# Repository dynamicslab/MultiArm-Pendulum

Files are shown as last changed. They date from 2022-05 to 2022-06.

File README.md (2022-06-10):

# The Experimental Multi-Arm Pendulum on a Cart

## Overview:
This repository is for our paper: "*[The Experimental Multi-Arm Pendulum on a Cart: A Benchmark System for Chaos, Learning, and Control.](https://arxiv.org/abs/2205.06231)*" The following figure shows an overview of the experimental system.

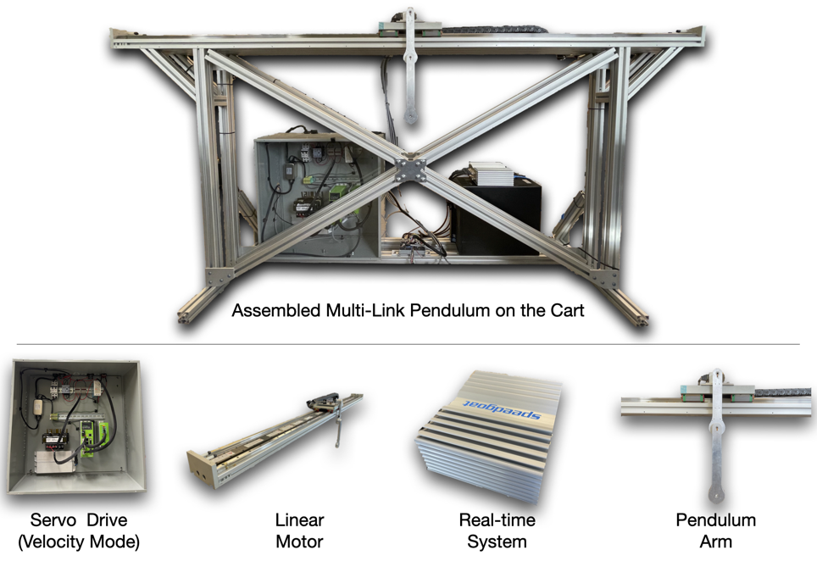
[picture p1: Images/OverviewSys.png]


This repository contains the following files:
- All the CAD files needed to build the pendulum hardware.
- Link to the user's manuals that correspond to some of the parts we used.
- The experimental data sets of the **single, double, and triple pendulum** with and without external excitation. We believe this data set will be extremely useful for the Machine Learning and AI community to test their modeling algorithm. The slow-motion video data for the double pendulum can be accessed using this **[Link](http://doi.org/10.5281/zenodo.6633719)**.
- A demo file for setting up the hardware system and using it for data collection.
- Demo files for parameter estimation of the **single, double, and triple pendulum**.

## Cite:
If you find our data set or hardware useful for your research, please kindly cite it as: 

@misc{kaheman2022experimental,
      title={The Experimental Multi-Arm Pendulum on a Cart: A Benchmark System for Chaos, Learning, and Control}, 
      author={Kadierdan Kaheman and Urban Fasel and Jason J. Bramburger and Benjamin Strom and J. Nathan Kutz and Steven L. Brunton},
      year={2022},
      eprint={2205.06231},
      archivePrefix={arXiv},
      primaryClass={nlin.CD}
}

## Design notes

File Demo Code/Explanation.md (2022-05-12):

# This folder contains files needed for data collection and control of the triple pendulum on the cart system.

This folder contains following files:
- EncoderReading.slx: This Simulink file is used to record the sensor data and control the linear motor.
- speedgoat_IO392_50k_CI_02385.mat: This is the Bitstream file needed to configure the Speedgoat system's IO-392 module.

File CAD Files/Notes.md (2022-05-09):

# Notes:

- The author thanks HIWIN for providing the CAD file of their linear motor. 
- Some CAD files are downloaded from McMaster.com, and the author does not claim any copyrights on those files.

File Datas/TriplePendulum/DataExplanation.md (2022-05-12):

# This folder contains the experimental data gathered from the triple pendulum system.

This folder contains following files:
- TripleDataFreeSwing_X_Dt_0_0001.mat: These files record the rotational angle and velocity of the triple pendulum with zero cart movement. The sampling rate is dt=0.0001(s).
- TripleDataWithControl_X_Dt_0_0001.mat: These files record the rotational angle and velocity of the triple pendulum with pendulum cart moving back and forth. The cart position and velocity are also recorded. The sampling rate is dt=0.0001(s).

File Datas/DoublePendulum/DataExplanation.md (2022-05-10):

# This folder contains data set of double pendulum.

- DoubleDataFreeSwing_X_Dt_0_001.mat: Those files contains the data set recorded during the double pendulum freee-swing experiments. Dring the experiments the pendulum cart is mounted and won't move. The angular position and velocity of the pendulum arm is recorded.
- DoubleDataWithControl_X_Dt_0_0001.mat: Those files contains the data set recorded during the double pendulum experiments with control input. Two extra measurements, pendulum cart position and velocity are given.

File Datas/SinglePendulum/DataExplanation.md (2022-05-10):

# This folder contains the experimental data of the single pendulum on the cart system.

This folder contains the following files:
- SingleDataFreeSwing_1_Dt_0_0001.mat: This file contains recordings of the free-swing experiment of the single pendulum. The sampling time is dt=0.0001, with the pendulum cart mounted.
- SingleDataWithControl_1_Dt_0_0001.mat: This file cintains the recording of the single pendulum on the cart system with the cart moving back and forth. The sampling time is dt=0.0001. The movement of the cart along wih its velocity is stored in the "Distance" and "Velocity" structure.
- SingleDataWithControl_2_Dt_0_0001.mat: This file cintains the recording of the single pendulum on the cart system with the cart moving back and forth. The sampling time is dt=0.0001. The movement of the cart along wih its velocity is stored in the "Distance" and "Velocity" structure.

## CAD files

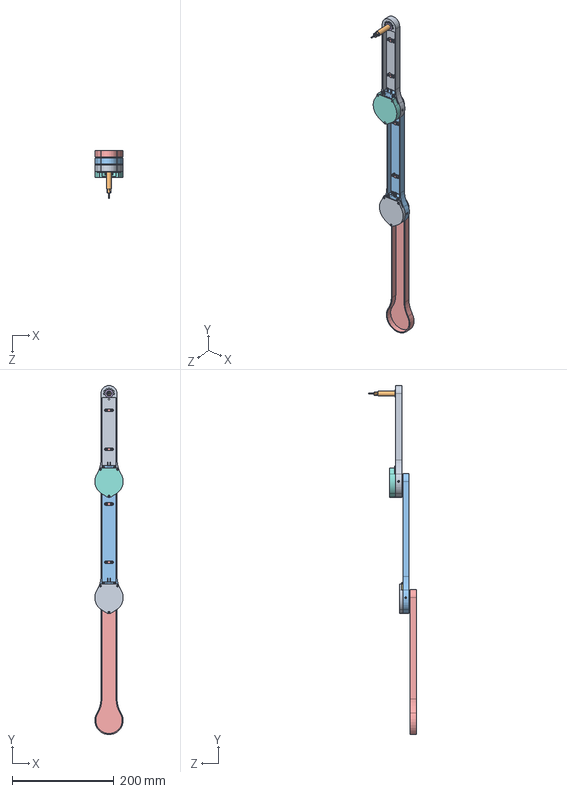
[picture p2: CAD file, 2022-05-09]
CAD Files/ArmsAssembly.SLDASM
55.9 x 686.3 x 93.5 mm
Arm1
Arm1Shaft
Arm2
Arm2Shaft
Arm3
Arm3Shaft
BearingPlate x 2
BrushBlock-5
BrushShim
EncoderShim x 2
SlipRing5Channel
SlipRing8Channel
WireClip x 4
91251A077_Black-Oxide Alloy Steel Socket Head Screw x 14
91251A081_Black-Oxide Alloy Steel Socket Head Screw x 4
3088A449_1008-1010 Carbon Steel Ring Shims x 2
R188 x 4
97022A213_316 Stainless Steel Ring Shim x 2
EM2-X-X-X x 2
HUBDISK-2-X-250-X x 2
98126A447_18-8 Stainless Steel Ring Shim x 2
98055A122_1074-1095 Spring Steel Ring Shim
97633A130_External Retaining Ring x 2
Arm1Cover
Arm2Cover

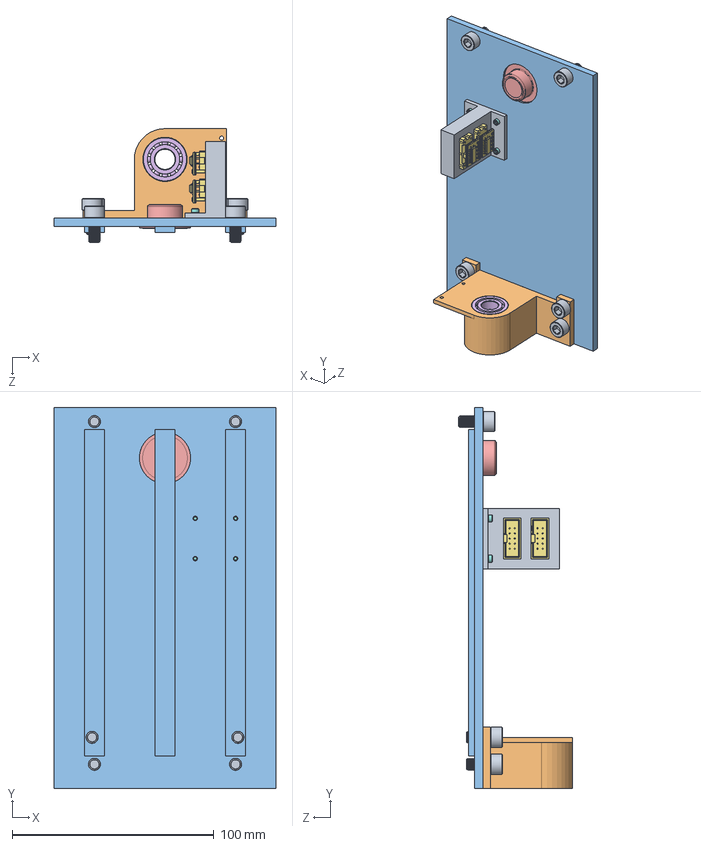
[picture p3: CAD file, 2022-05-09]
CAD Files/CartPlateAssemble.SLDASM
110.0 x 189.0 x 56.5 mm
DriverClip
BearingHousing
CartPlate
Spacer
3329A31_Surface-Mount Circular Mountable Level
5972K241_Ball Bearing x 2
PC4-H10_SolidWorks x 2
91251A077_Black-Oxide Alloy Steel Socket Head Screw x 4
96144A111_Fine-Thread Alloy Steel Socket Head Screw x 6

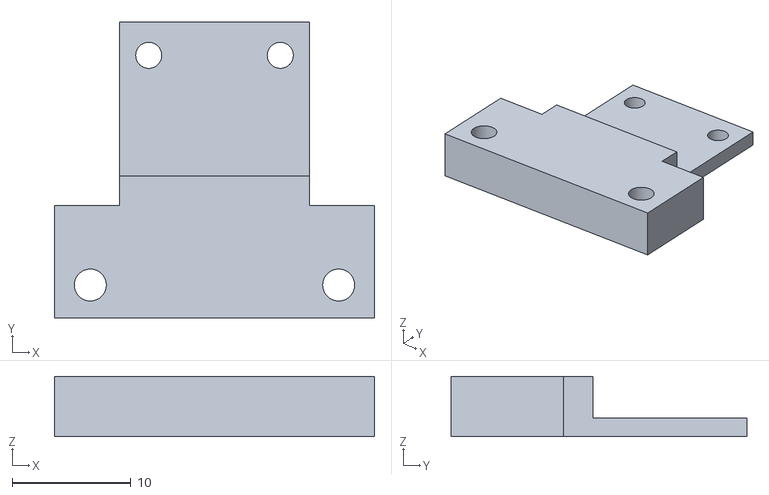
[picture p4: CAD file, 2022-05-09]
CAD Files/3D Printed Parts/BlockBase.STL
27.0 x 25.0 x 5.08

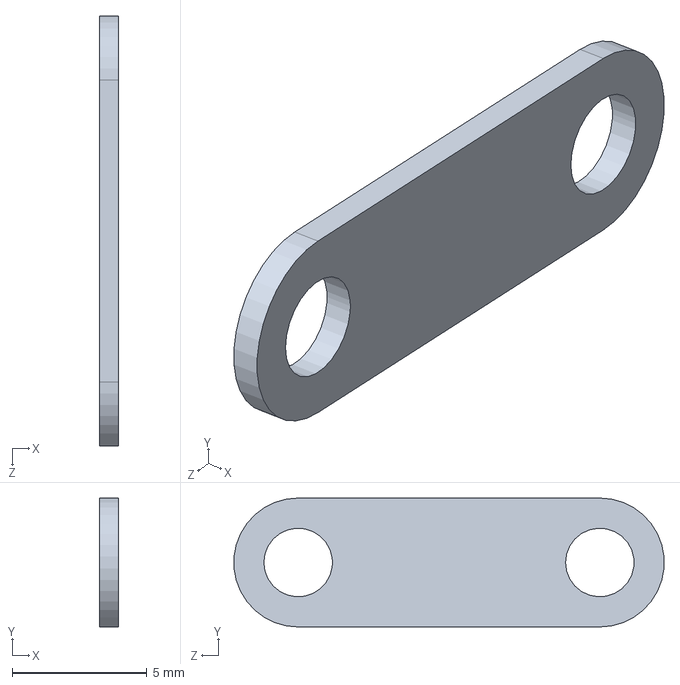
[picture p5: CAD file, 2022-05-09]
CAD Files/Parts/BrushShim.SLDPRT
0.711 x 4.78 x 15.9 mm

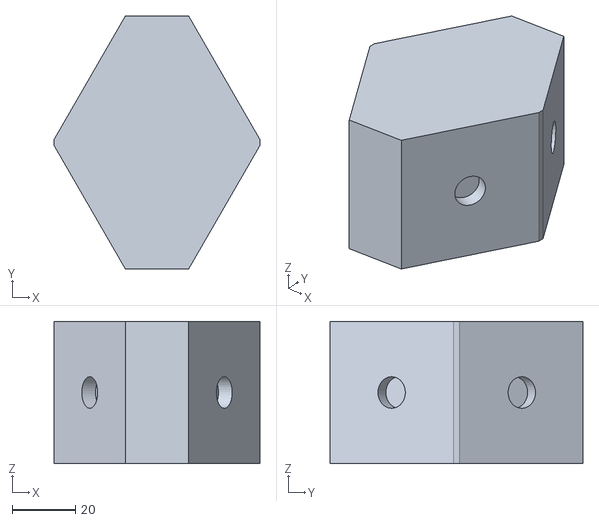
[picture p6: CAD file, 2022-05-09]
CAD Files/3D Printed Parts/AlignTool2.STL
65.0 x 79.9 x 45.0

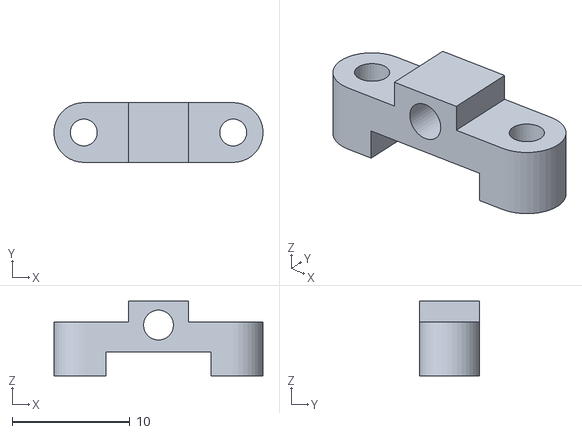
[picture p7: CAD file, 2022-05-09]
CAD Files/3D Printed Parts/WireClip.STL
17.8 x 5.08 x 6.35

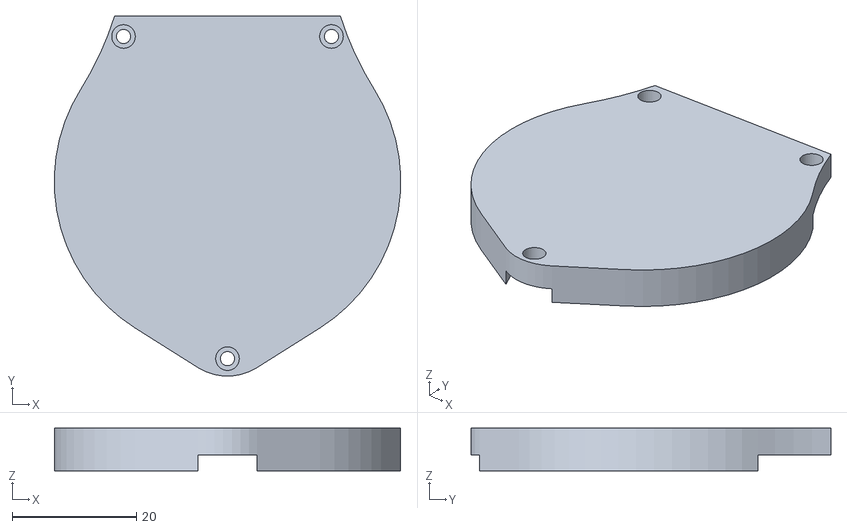
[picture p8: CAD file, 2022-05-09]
CAD Files/3D Printed Parts/Arm2Cover.STL
55.8 x 58.0 x 6.86

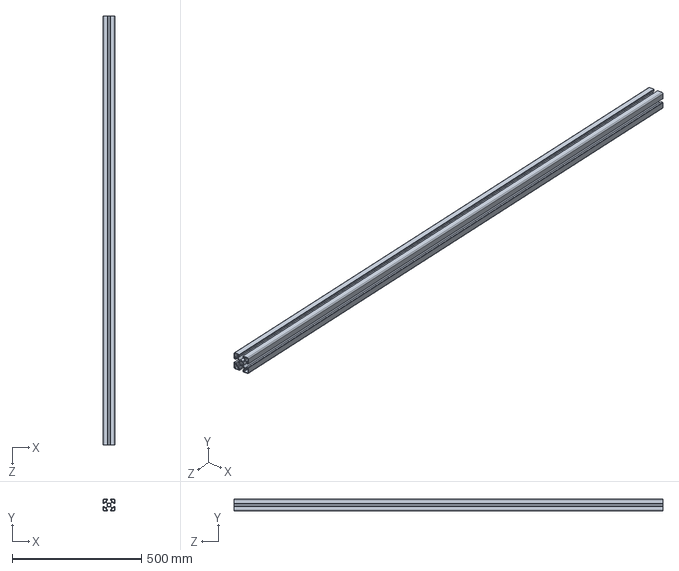
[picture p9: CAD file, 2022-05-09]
CAD Files/Parts/Extrusion6.SLDPRT
45.0 x 45.0 x 1658.5 mm

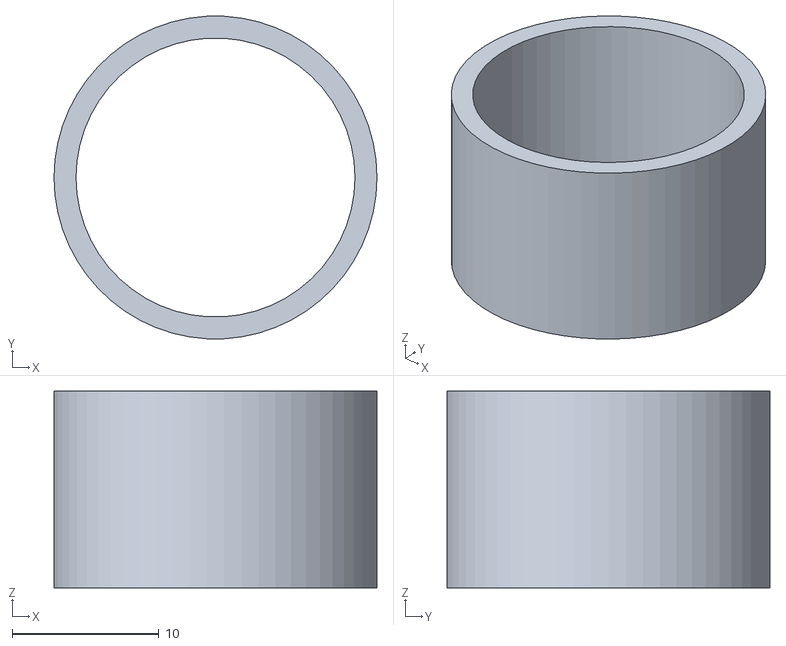
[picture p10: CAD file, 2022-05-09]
CAD Files/3D Printed Parts/Spacer.STL
22.0 x 22.0 x 13.4

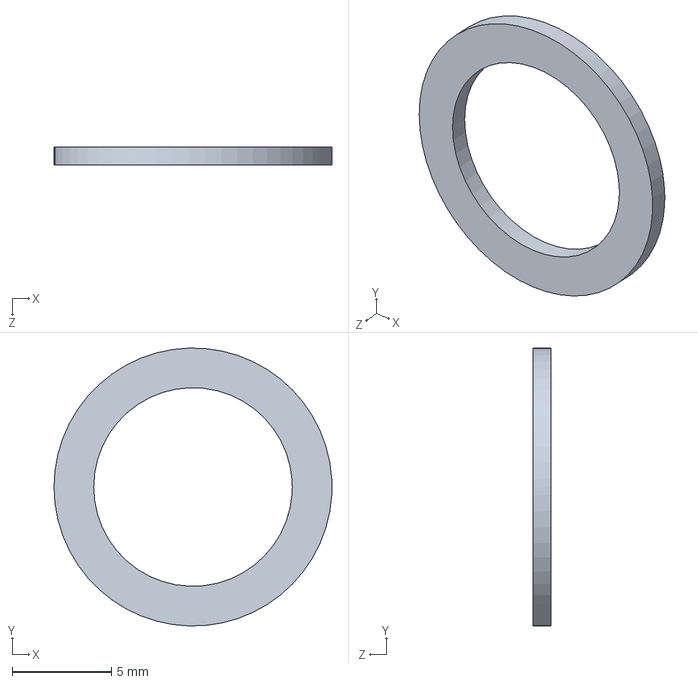
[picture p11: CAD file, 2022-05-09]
CAD Files/Parts/3DPrintedShim.SLDPRT
14.0 x 14.0 x 0.93 mm

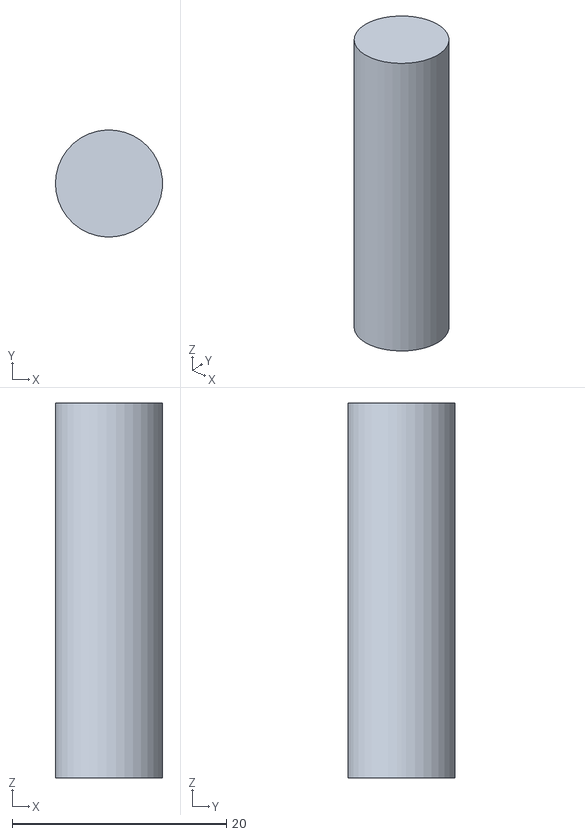
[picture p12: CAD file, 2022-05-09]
CAD Files/3D Printed Parts/AlignTool1.STL
10.0 x 9.99 x 35.0

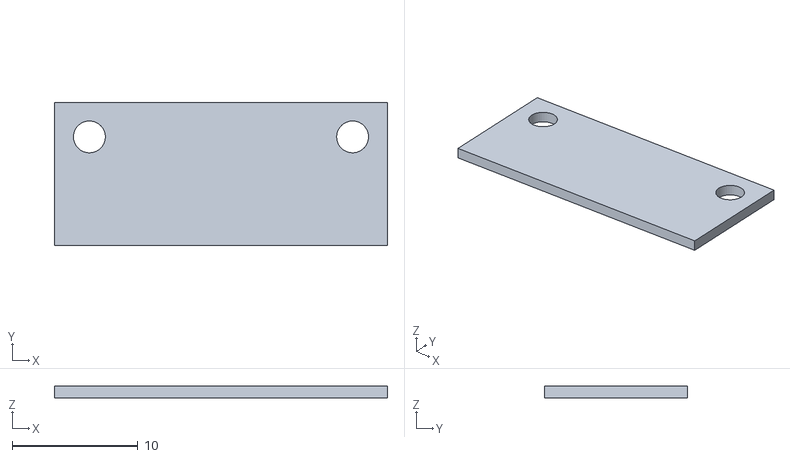
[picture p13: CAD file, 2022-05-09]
CAD Files/3D Printed Parts/EncoderShim.STL
26.5 x 11.4 x 0.965

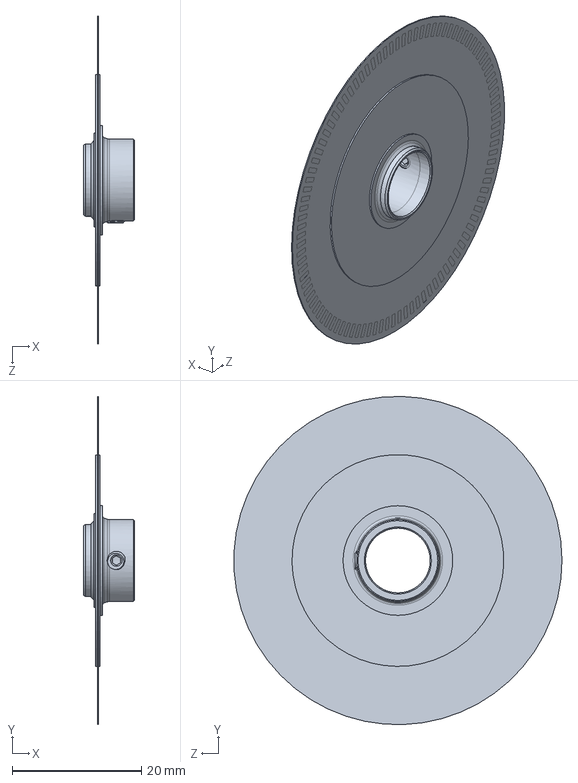
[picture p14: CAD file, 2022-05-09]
CAD Files/Parts/HUBDISK-2-X-394-X.SLDPRT
7.87 x 50.8 x 50.8 mm

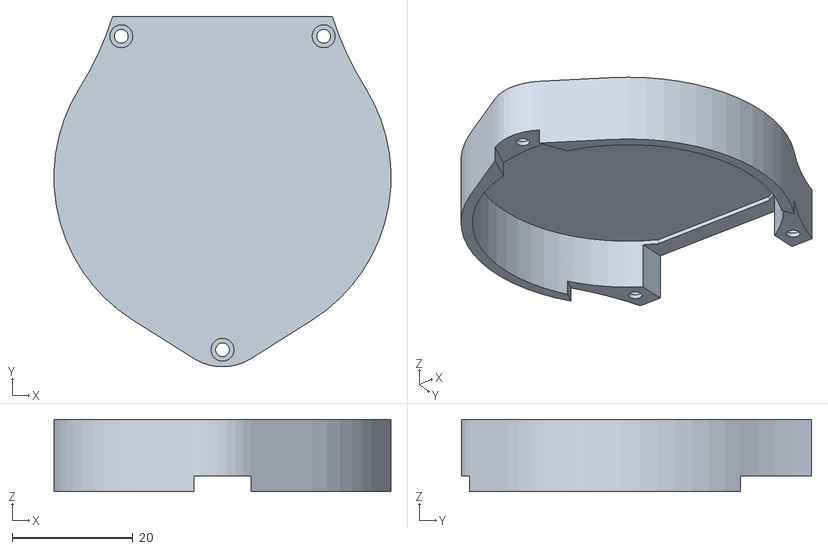
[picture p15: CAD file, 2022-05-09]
CAD Files/3D Printed Parts/Arm1Cover.STL
55.8 x 58.0 x 11.9

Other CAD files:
CAD Files/3D Printed Parts/DriverClip.STL
CAD Files/3D Printed Parts/BrushShim.STL
CAD Files/Parts/Arm3.SLDPRT
CAD Files/Parts/R188.SLDPRT
CAD Files/Drawing/Arm1.SLDDRW
CAD Files/Drawing/Arm1Shaft.SLDDRW
CAD Files/Drawing/Arm2.SLDDRW
CAD Files/Drawing/Arm2Shaft.SLDDRW
CAD Files/Drawing/Arm3.SLDDRW
CAD Files/Drawing/Arm3Shaft.SLDDRW
CAD Files/Drawing/BearingHousing.SLDDRW
CAD Files/Drawing/BearingPlate.SLDDRW
CAD Files/Drawing/CartPlate.SLDDRW
CAD Files/Drawing/XConnector.SLDDRW
CAD Files/Parts/3088A449_1008-1010 Carbon Steel Ring Shims.SLDPRT
CAD Files/Parts/3329A31_Surface-Mount Circular Mountable Level.SLDPRT
CAD Files/Parts/47065T83_70 lb. Capacity Plate Mount Swivel Caster for T-Slotted Framing.SLDPRT
CAD Files/Parts/47065T948_T-Slotted Framing (1).SLDPRT
CAD Files/Parts/47065T998_T-Slotted Framing.SLDPRT
CAD Files/Parts/5537T134_T-Slotted Framing.SLDPRT
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

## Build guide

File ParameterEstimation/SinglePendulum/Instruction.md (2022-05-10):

# This folder contains the files for the parameter estimation of the single pendulum.

The purpose of the files are listed as follows:
- SinglePendulumArm_RawData_1.mat: This is the raw data we collected from the single pendulum free-swing experiment. During the experiments, the cart of the pendulum is fixed and the rotational angle and velocity of the pendulum arm is recorded. The first signal of the "data" structure is the rotational angle, while the second one represents the rotational velocity.
- PrepareDataForSinglePendulumParameterEstimation.m: This file process the above raw data and trim it into the correct format for parameter estimation. Moreover, it also allows the user to perform nosie filtering on the velocity data of the single pendulum. The this script will generate a file named "SinglePendulumDataForParameterEstimation.mat", which will be used for parameter estimation.
- SinglePendulumDataForParameterEstimation.mat: Mat file generated by above script. This mat file contains the data that will be used for parameter estimation and validation.
- OptimizeParameter_SinglePendulum.mlx: This script is used to solve the optimization problem that identifies the parameters of the single pendulum.
- ObjectiveFuntion_SinglePendulumParameterEstimation.m: This file define the optimization problem needed for the parameter estimation of the single pendulum.
- EstimatedParameters_SinglePendulum.mat: This files contains the estimated parameters of the single pendulum. For details on the meaning of the values and its units, please check the "OptimizeParameter_SinglePendulum.mlx" file.
- SinglePendulumSymbolicCalculation.m: This file derives the equation of motion of the single pendulum. The derived ODE will be used for parameter estimation.
- SinglePendulumODE.m: This file is the derived ODE of the single pendulum.

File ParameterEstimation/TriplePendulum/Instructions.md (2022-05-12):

# This folder contains files for the parameter estimation of the triple pendulum.

This folder contains following files:
- TriplePendulumData_Raw.mat: Experimental data gather from the triple pendulum free-swing moton, with sampling rate of dt=0.001. This file will be processed by "PrepareDataForTriplePendulumParameterEstimation.m" to get rid of the noise in the derivative measurements. Then it will be trimed into pieces and stored into a cell array.
- PrepareDataForTriplePendulumParameterEstimation.m: This file is used to process the "TriplePendulumData_Raw.mat" file so that it can be used for parameter estimation.
- TriplePendulumSymbolicCalculation.m: This file is usd to calculate the ODE of the triple pendulum via symbolic toolbox of Matlab.
- TriplePendulumODE_Mounted.m: This file is the ODE file of the triple pendulum. It can used used to simulate the behavior of the triple pendulum.
- TriplePendulumSimWithX0.m: This file is used to simulate the ODE of the triple pendulum given some user define initial condition of triple pendulum.
- ObjectiveFuntion_TriplePendulumParameterEstimation.m: This file is used to define the objective function of the parameter estimation problem of the triple pendulum.
- OptimizeParameter_TriplePendulum.mlx: This file is used to solve the prameter estimation problem of the triple pndulum. It will also save the estimated parameters of the triple pendulum.
-  EstimatedParameters_TriplePendulum.mat: This file stores the estimated parameters of the triple pendulum. For their meaning, please check the "OptimizeParameter_TriplePendulum.mlx" file.

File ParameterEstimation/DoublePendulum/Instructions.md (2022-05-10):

# This folder contains files for estimating the parameters of double pendulum.

The files contained in this folders are:
- DoublePendulumData_Raw.mat: The raw data collected from the double pendulum free-swing experiments. The sampling rate used is dt=0.001s and the pendulum cart is mounted when recording the data. This file is used by "PrepareDataForDoublePendulumParameterEstimation.m" to generated processed double pendulum data for parameter estimation.
- PrepareDataForDoublePendulumParameterEstimation.m: This file is used to chop the raw double pendulum data into pieces. Those pieces of data are stored into a cell array for parameter estimation and validation. The training data and validation data are stored in the "DoublePendulumDataForParameterEstimation.mat" file.
- DoublePendulumDataForParameterEstimation.mat: The data used for parameter estimation and validation.
- ObjectiveFuntion_DoublePendulumParameterEstimation.m: The objective function for the parameter estimation.
- OptimizeParameter_DoublePendulum.mlx: The Matlab script that solves the parameter estimation problem.
- DoublePendulumODE_Mounted.m: The ODE files for simulating the mounted double pendulum. This file is used in the objection file.
- EstimatedParameters_DoublePendulum.mat: The estimated values of double pendulum arm's parameters.
- DoublePendulumSymbolicCalculation.m: The symbolic calculation file needed for deriving the ODEs of double pendulum.

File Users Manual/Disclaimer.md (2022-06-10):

# The author does not claim copyrights on the documentation/user manual shown in this folder. All right belongs to the manufacturer who wrote those documentations. Those files are downloaded from the product's website.

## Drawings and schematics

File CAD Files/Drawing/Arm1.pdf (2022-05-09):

0.433

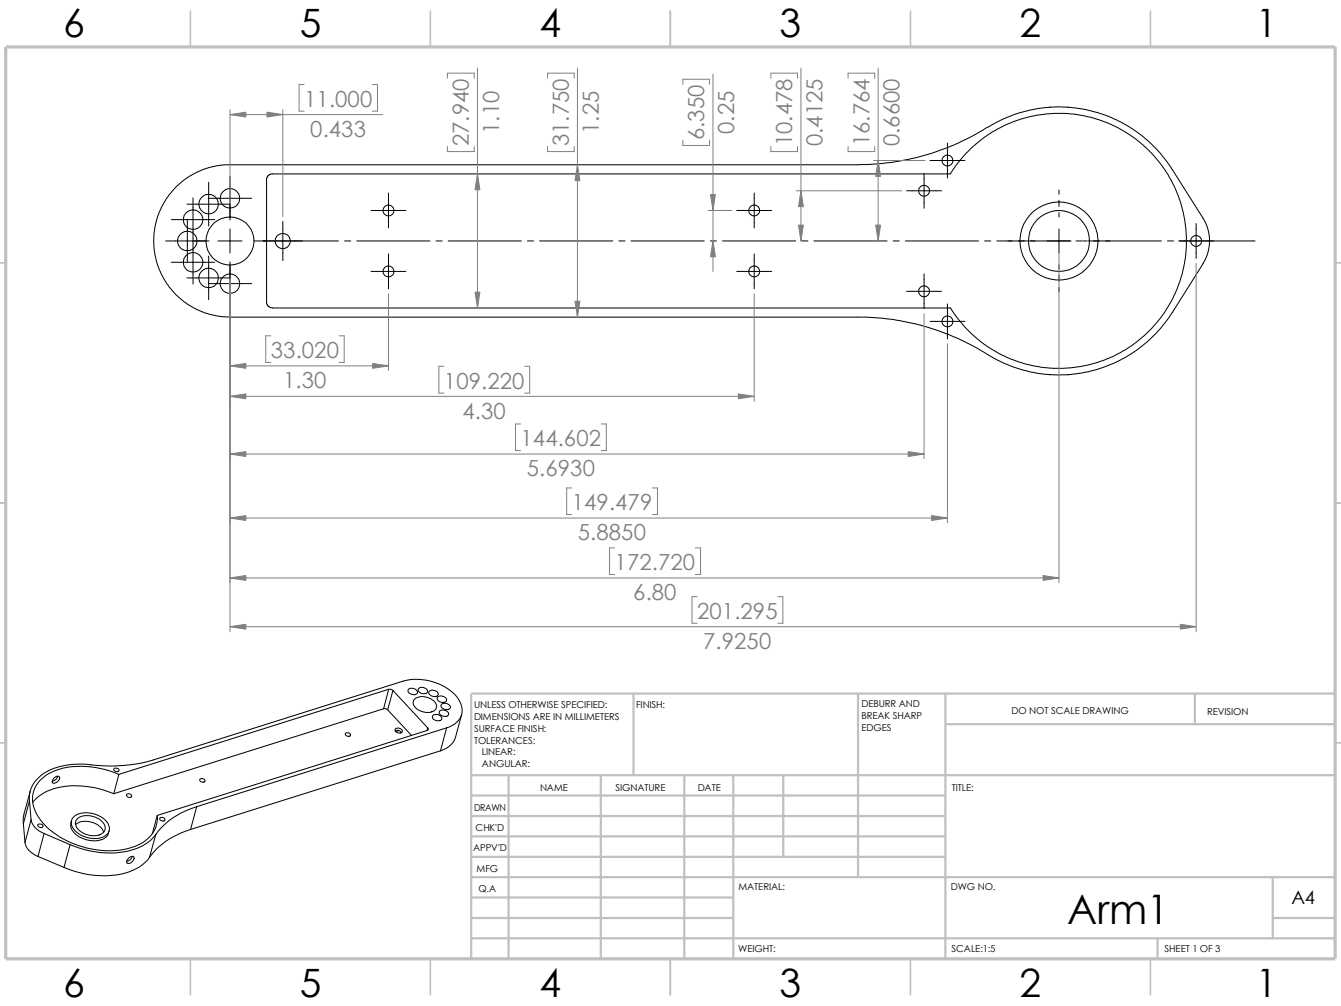
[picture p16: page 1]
REVISION; SCALE:1:5; SHEET 1 OF 3; WEIGHT:; EDGES; FINISH:; DEBURR AND BREAK SHARP; Arm1 ³¹.750

UNLESS OTHERWISE SPECIFIED:
DIMENSIONS ARE IN MILLIMETERS
SURFACE FINISH:
TOLERANCES:
LINEAR:
ANGULAR:

DO NOT SCALE DRAWING

NAME | SIGNATURE | DATE | | | | TITLE:

DRAWN
CHK'D
APPV'D

MFG
Q.A | | | | MATERIAL: | DWG NO. | A4

A A

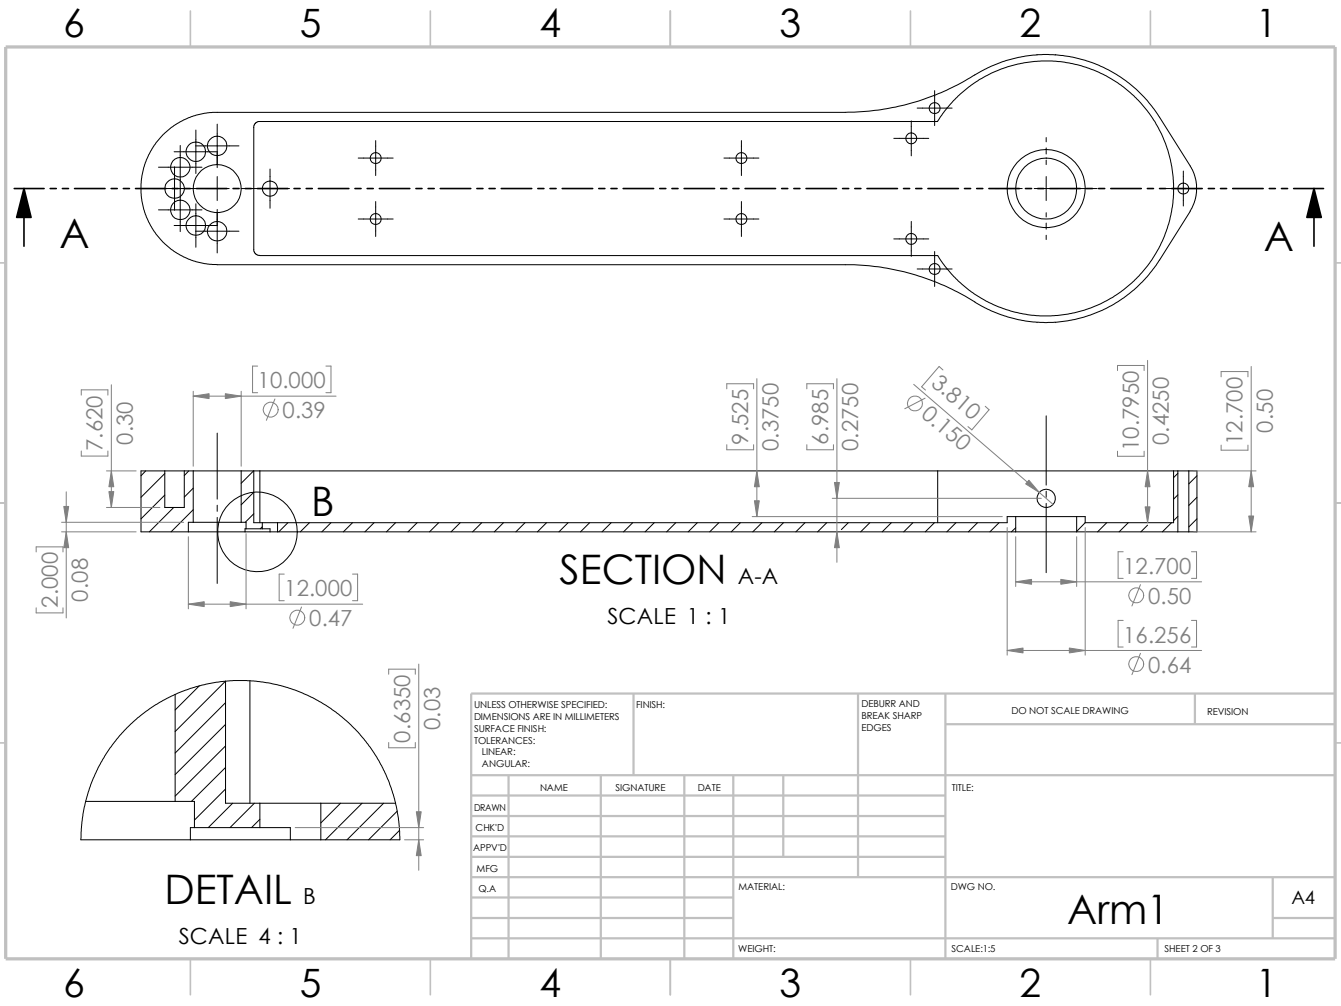
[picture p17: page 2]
DETAIL B; SCALE 4 : 1; SECTION A-A; SCALE; FINISH:; EDGES; DO NOT SCALE DRAWING; REVISION; SCALE:1:5; WEIGHT:; SHEET 2 OF 3; APPV'D; DEBURR AND BREAK SHARP

UNLESS OTHERWISE SPECIFIED:
DIMENSIONS ARE IN MILLIMETERS
SURFACE FINISH:
TOLERANCES:
LINEAR:
ANGULAR:

NAME | SIGNATURE | DATE | TITLE:

CHK'D DRAWN

MFG
Q.A | MATERIAL: | DWG NO. Arm1 | A4

# Uniformly Distributed

# For 2-56 Bolts

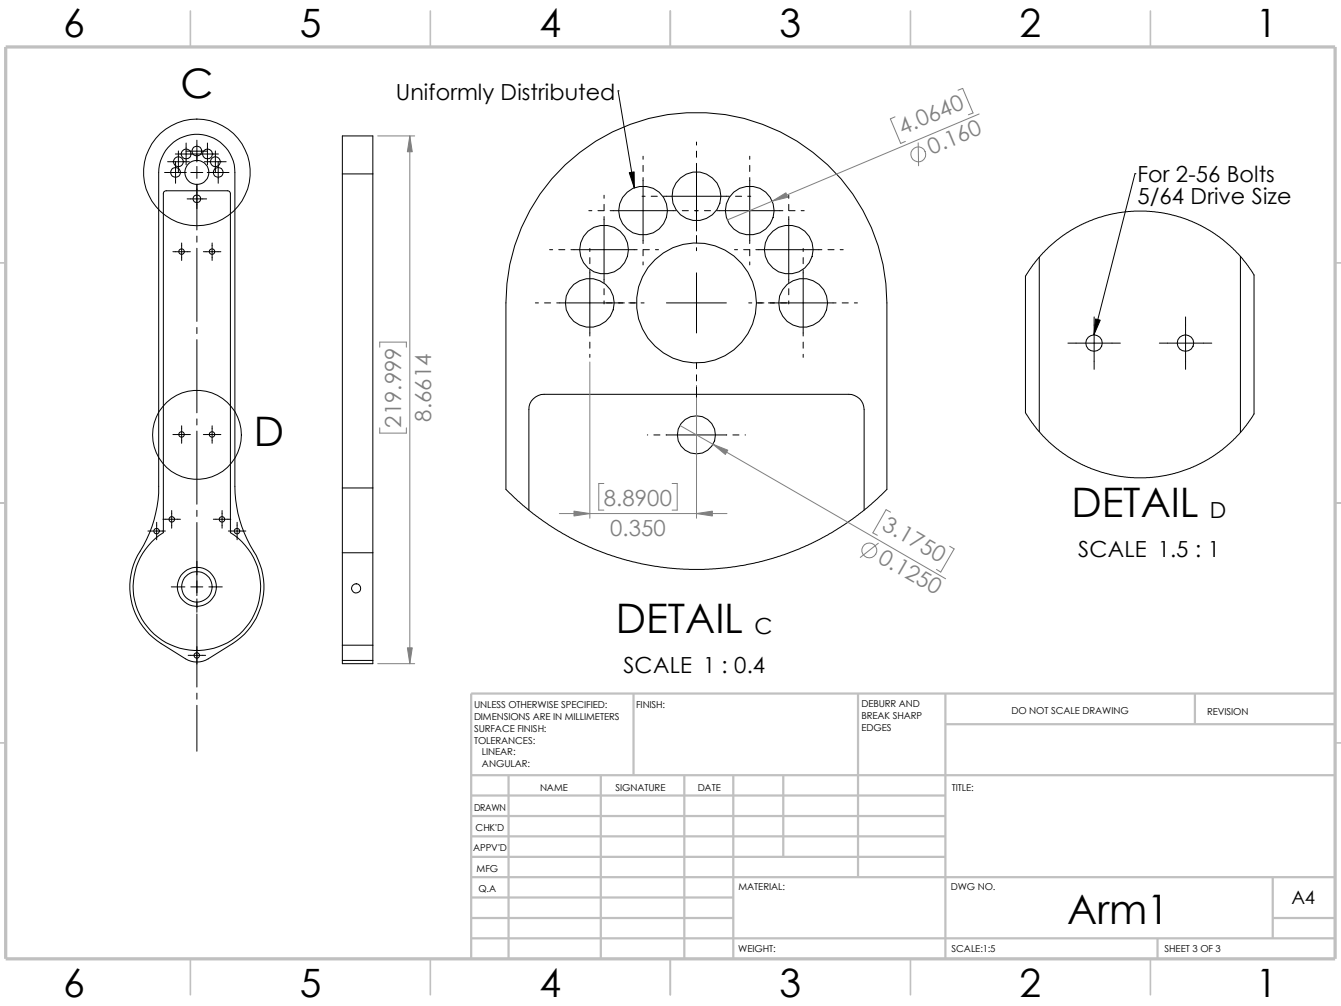
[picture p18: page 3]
SCALE 1 : 0.4; DETAIL C; SCALE; DETAIL; 5/64 Drive Size; REVISION; SHEET 3 OF 3; WEIGHT:; SCALE:1:5; FINISH:; EDGES; DEBURR AND BREAK SHARP; Arm1 ²¹⁹.999

UNLESS OTHERWISE SPECIFIED:
DIMENSIONS ARE IN MILLIMETERS
SURFACE FINISH:
TOLERANCES:
LINEAR:
ANGULAR:

DO NOT SCALE DRAWING

NAME | SIGNATURE | DATE | | | | TITLE:

DRAWN
CHK'D
APPV'D

MFG
Q.A | | | | MATERIAL: | DWG NO. | A4

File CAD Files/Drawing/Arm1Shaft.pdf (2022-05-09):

6

5

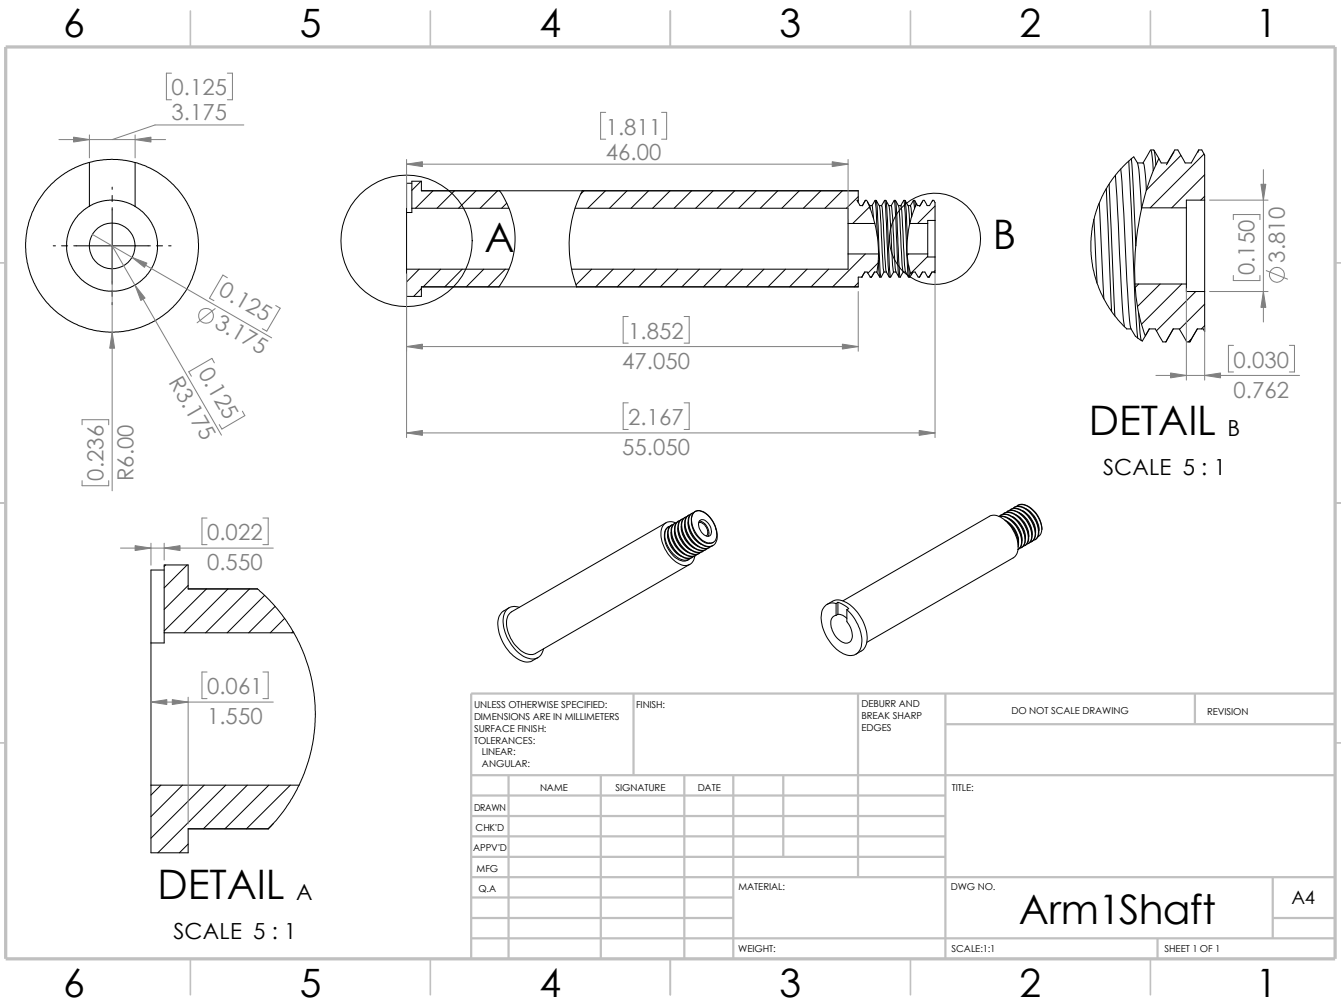
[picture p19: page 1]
WEIGHT:; SCALE:1:1; SHEET 1 OF 1; REVISION; FINISH:; EDGES; DEBURR AND BREAK SHARP; DETAIL A; SCALE 5 : 1; DETAIL B

DO NOT SCALE DRAWING UNLESS OTHERWISE SPECIFIED:
DIMENSIONS ARE IN MILLIMETERS
SURFACE FINISH:
TOLERANCES:
LINEAR:
ANGULAR:

NAME | SIGNATURE | DATE | | | | TITLE:

DRAWN
CHK'D
APPV'D
Q.A | | | | MATERIAL: | DWG NO. Arm1Shaft | A4

MFG

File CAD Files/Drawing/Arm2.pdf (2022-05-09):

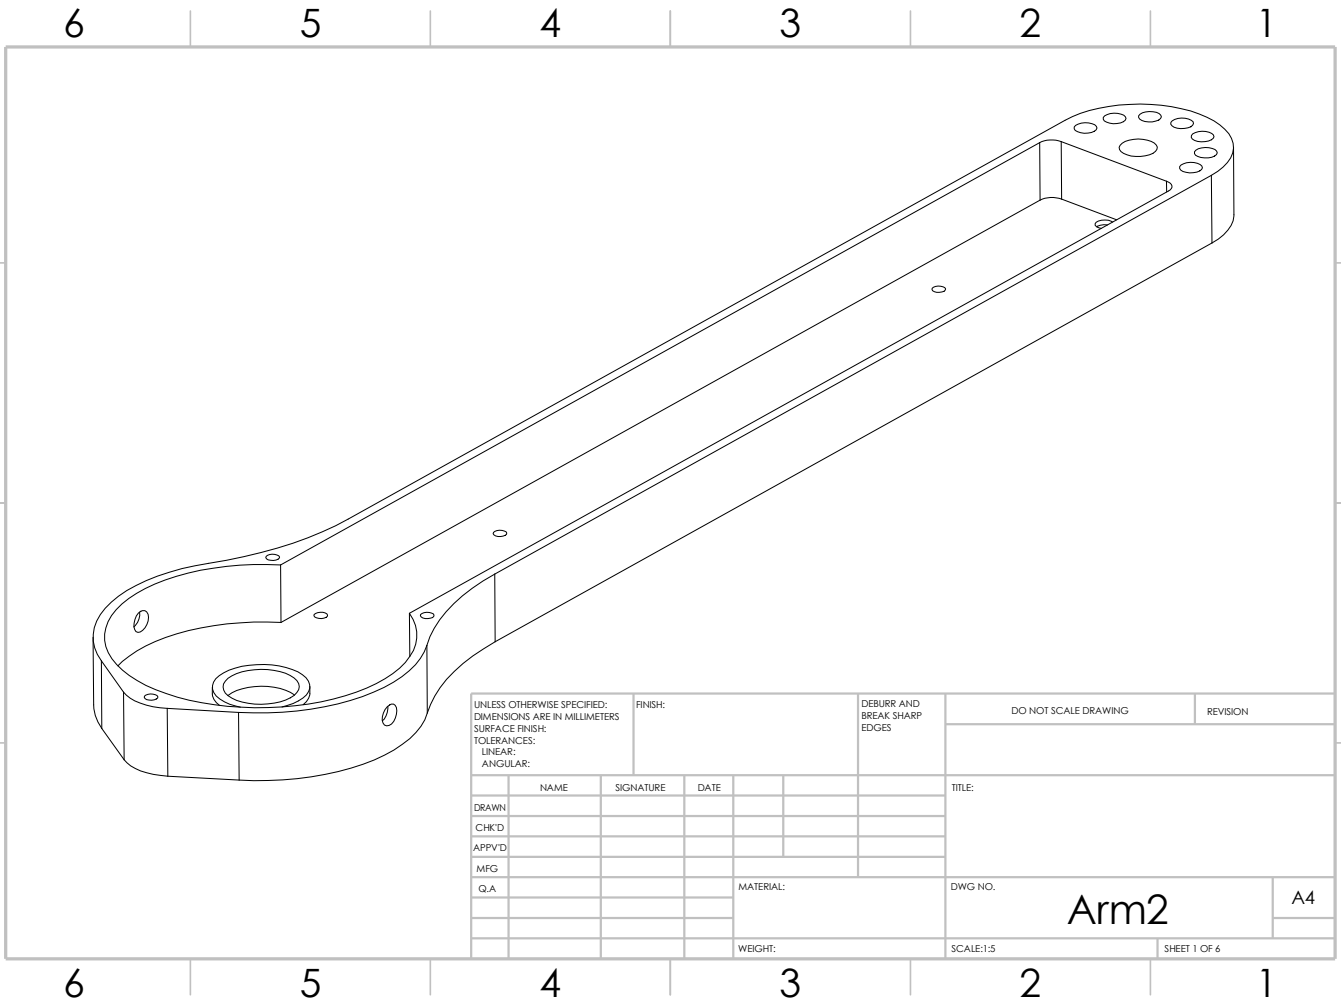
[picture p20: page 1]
FINISH:; DEBURR AND; BREAK SHARP EDGES; DO NOT SCALE DRAWING; REVISION; SCALE:1:5; SHEET 1 OF 6; WEIGHT:

UNLESS OTHERWISE SPECIFIED:
DIMENSIONS ARE IN MILLIMETERS
SURFACE FINISH:
TOLERANCES:
LINEAR:
ANGULAR:

NAME | SIGNATURE | DATE | | | | TITLE:

DRAWN
CHK'D
APPV'D

MFG
Q.A | | | | MATERIAL: | DWG NO. Arm2 | A4

# Through Hole

0.64

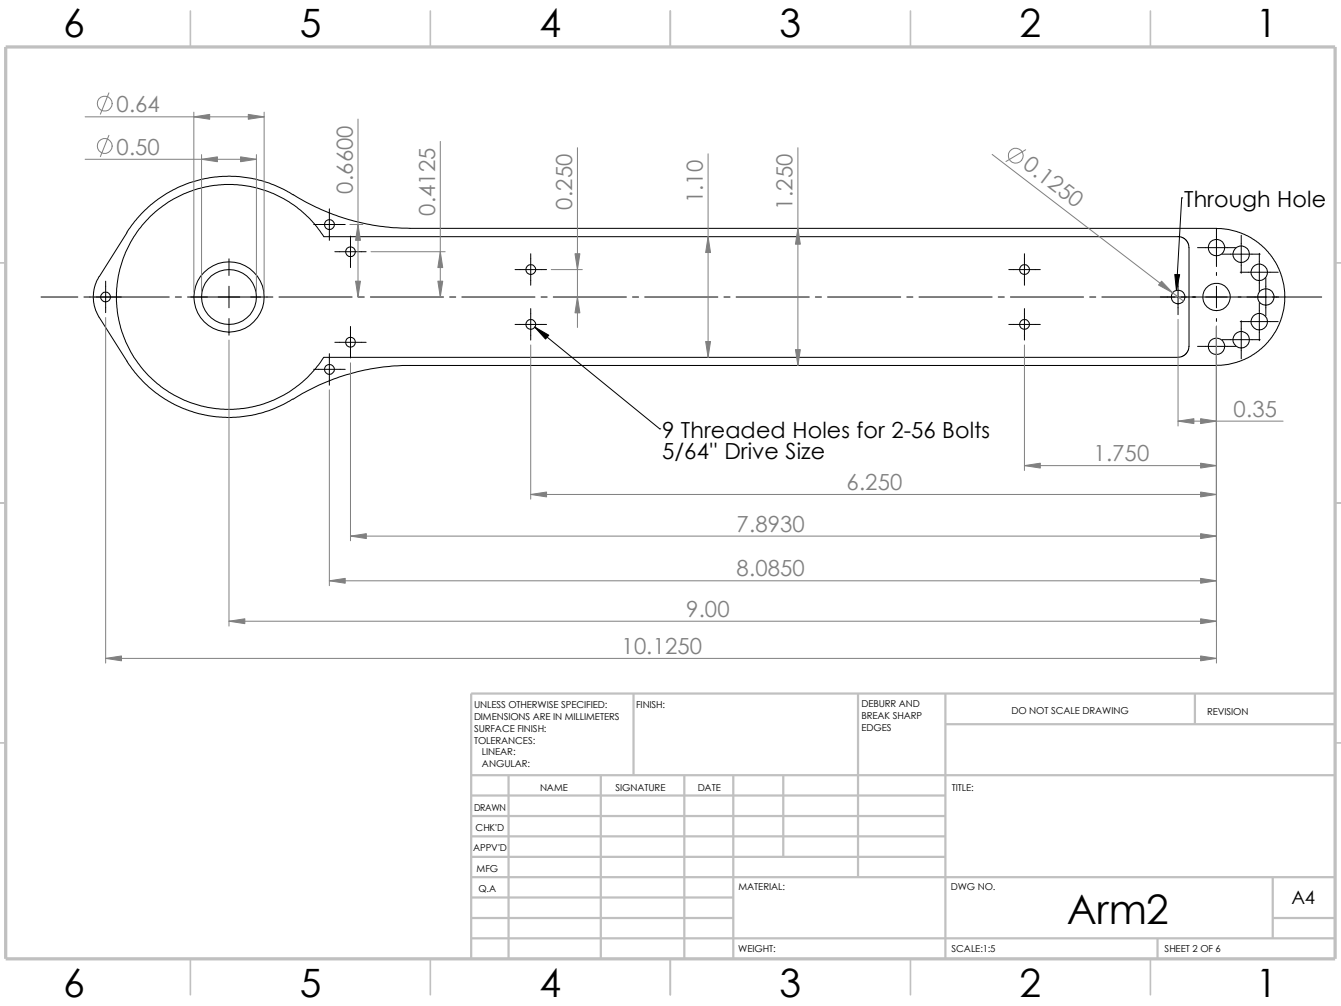
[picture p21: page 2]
FINISH:; DEBURR AND; BREAK SHARP EDGES; DO NOT SCALE DRAWING; REVISION; SCALE:1:5; SHEET 2 OF 6

9 Threaded Holes for 2-56 Bolts
5/64'' Drive Size

UNLESS OTHERWISE SPECIFIED:
DIMENSIONS ARE IN MILLIMETERS
SURFACE FINISH:
TOLERANCES:
LINEAR:
ANGULAR:

NAME | SIGNATURE | DATE | | | | TITLE:

DRAWN
CHK'D
APPV'D

MFG
Q.A | | | | MATERIAL: | DWG NO. Arm2 | A4

A

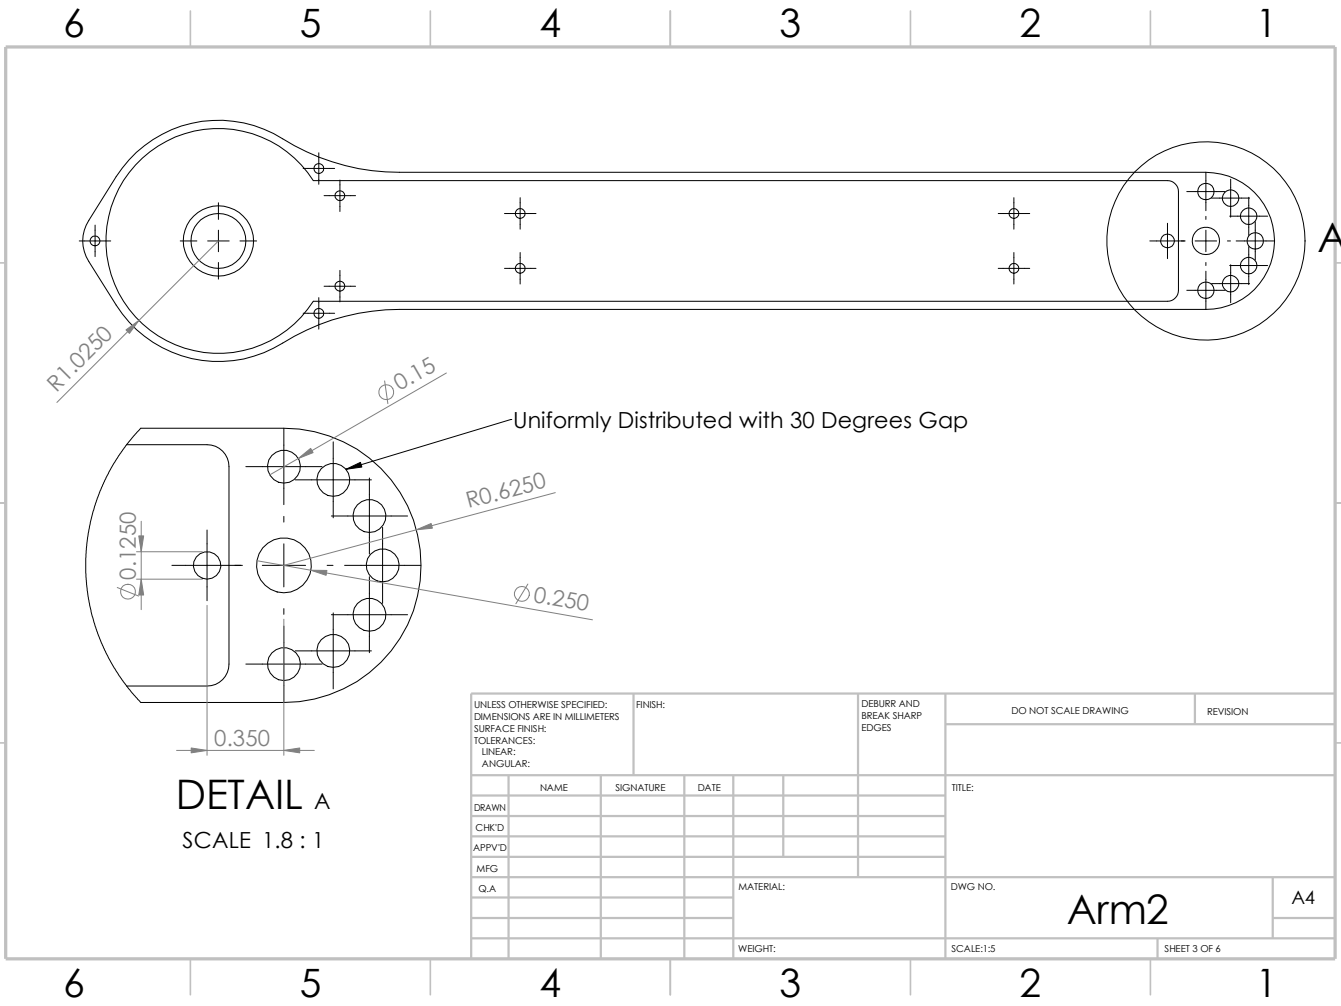
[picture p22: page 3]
FINISH:; DEBURR AND; BREAK SHARP EDGES; DO NOT SCALE DRAWING; REVISION; SCALE:1:5; SHEET 3 OF 6; SCALE 1.8 : 1; DETAIL A

Uniformly Distributed with 30 Degrees Gap

UNLESS OTHERWISE SPECIFIED:
DIMENSIONS ARE IN MILLIMETERS
SURFACE FINISH:
TOLERANCES:
LINEAR:
ANGULAR:

NAME | SIGNATURE | DATE | | | | TITLE:

DRAWN
CHK'D
APPV'D

MFG
Q.A | | | | MATERIAL: | DWG NO. Arm2 | A4

B B

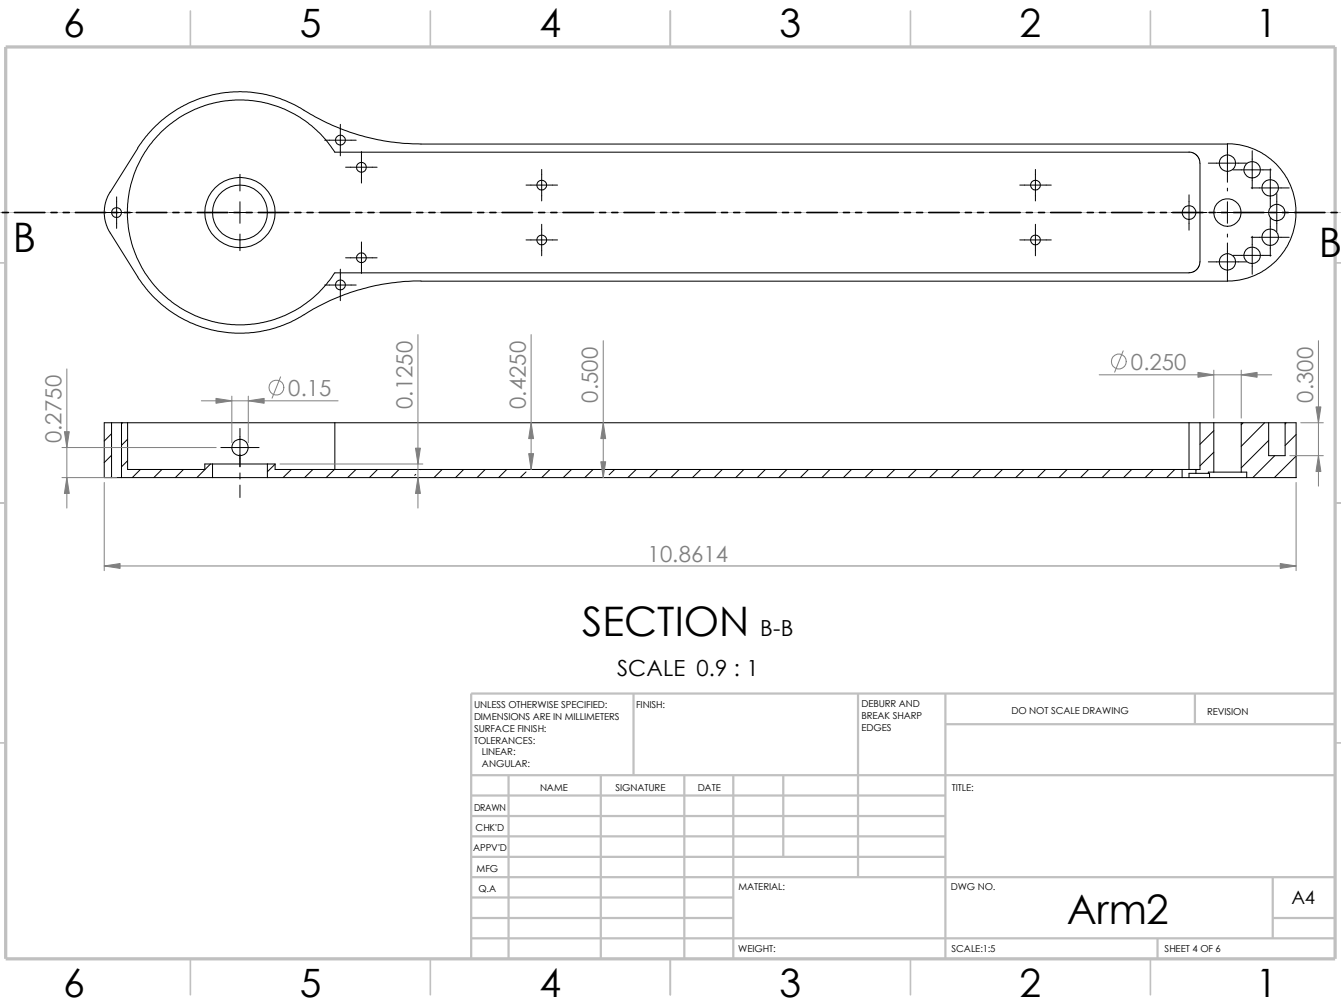
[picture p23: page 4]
FINISH:; DEBURR AND; BREAK SHARP EDGES; DO NOT SCALE DRAWING; REVISION; SCALE:1:5; SHEET 4 OF 6; SECTION B-B; SCALE 0.9 : 1

UNLESS OTHERWISE SPECIFIED:
DIMENSIONS ARE IN MILLIMETERS
SURFACE FINISH:
TOLERANCES:
LINEAR:
ANGULAR:

NAME | SIGNATURE | DATE | | | | TITLE:

DRAWN
CHK'D
APPV'D

MFG
Q.A | | | | MATERIAL: | DWG NO. Arm2 | A4

SCALE 0.8 : 1 ⁰.250 | 0.350

C

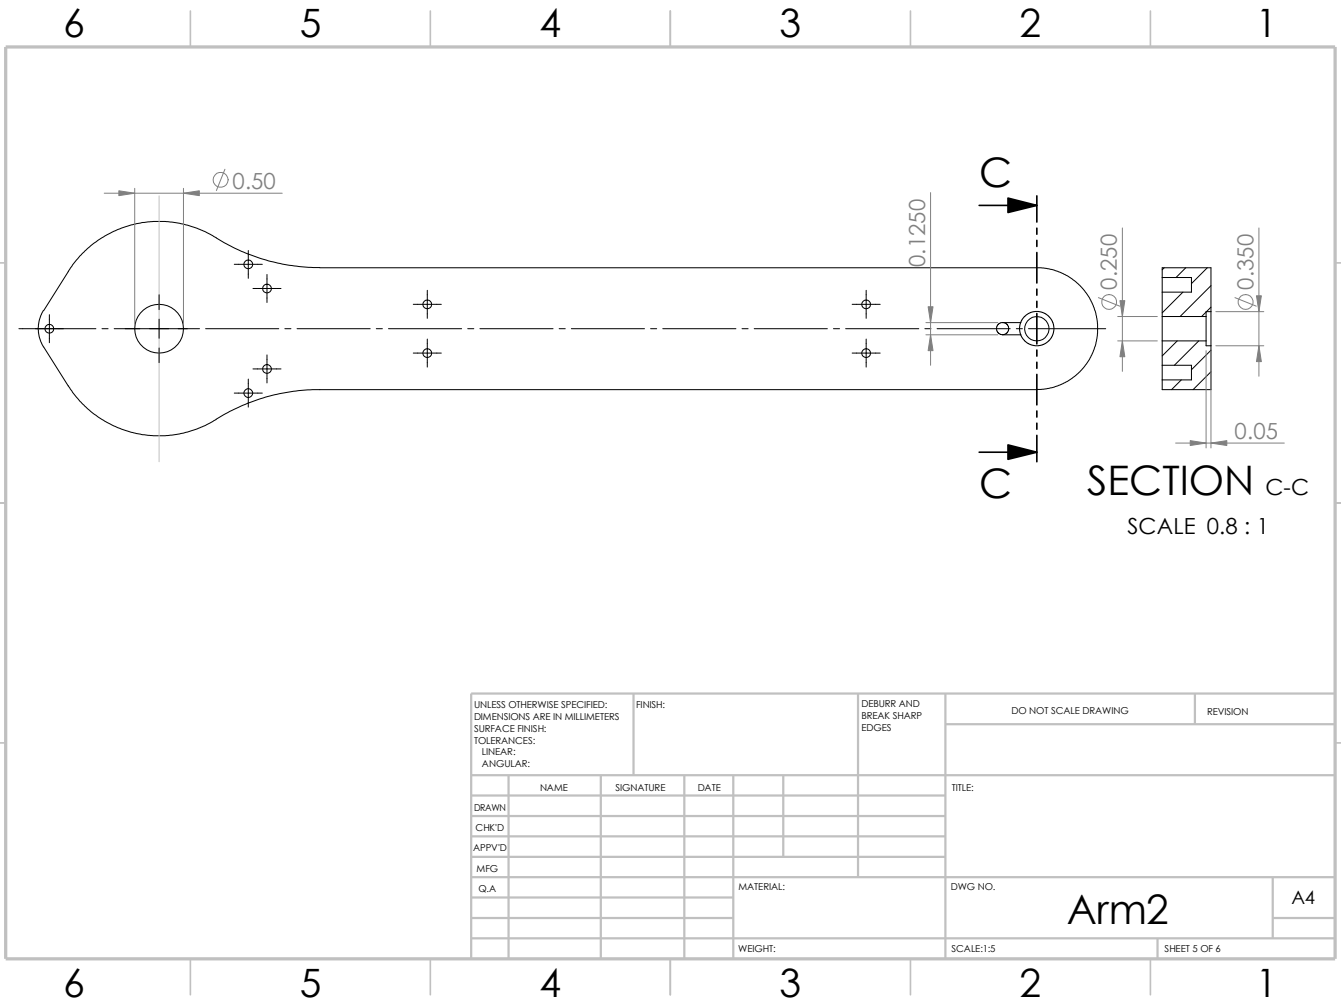
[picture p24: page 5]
FINISH:; DEBURR AND; BREAK SHARP EDGES; DO NOT SCALE DRAWING; REVISION; SCALE:1:5; SHEET 5 OF 6; SECTION C-C

UNLESS OTHERWISE SPECIFIED:
DIMENSIONS ARE IN MILLIMETERS
SURFACE FINISH:
TOLERANCES:
LINEAR:
ANGULAR:

NAME | SIGNATURE | DATE | | | | TITLE:

DRAWN
CHK'D
APPV'D

MFG
Q.A | | | | MATERIAL: | DWG NO. Arm2 | A4

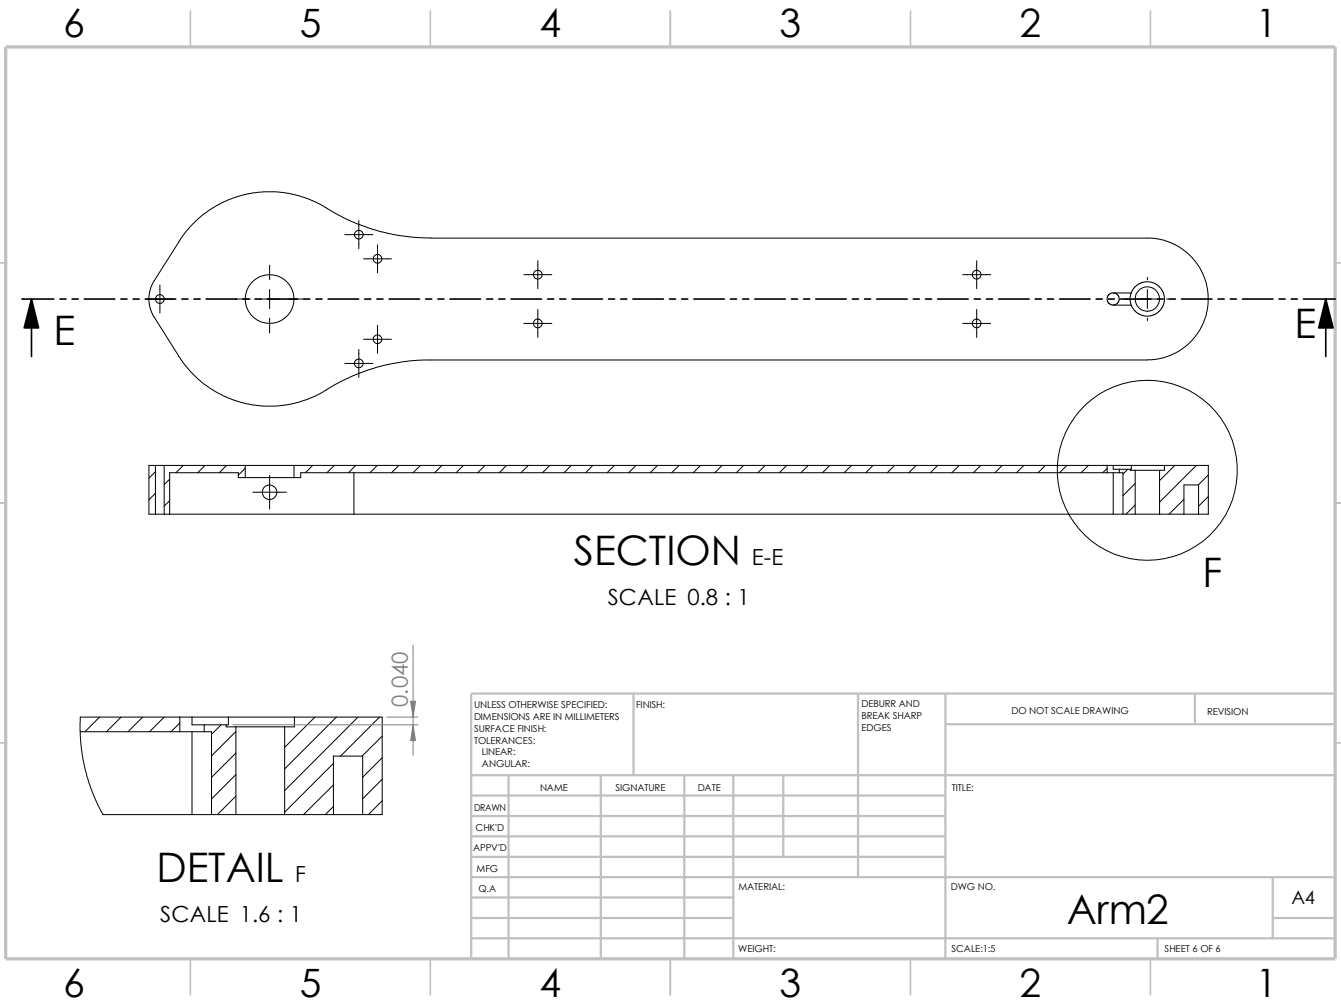
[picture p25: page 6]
CHK'D; FINISH:; DEBURR AND; BREAK SHARP EDGES; DO NOT SCALE DRAWING; REVISION; SCALE:1:5; SHEET 6 OF 6; SECTION E-E; SCALE 0.8 : 1; DETAIL F; SCALE 1.6 : 1

UNLESS OTHERWISE SPECIFIED:
DIMENSIONS ARE IN MILLIMETERS
SURFACE FINISH:
TOLERANCES:
LINEAR:
ANGULAR:

NAME | SIGNATURE | DATE | TITLE:

DRAWN

APPV'D

MFG
Q.A | MATERIAL: | DWG NO. Arm2 | A4

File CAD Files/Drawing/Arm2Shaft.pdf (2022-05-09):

6

5

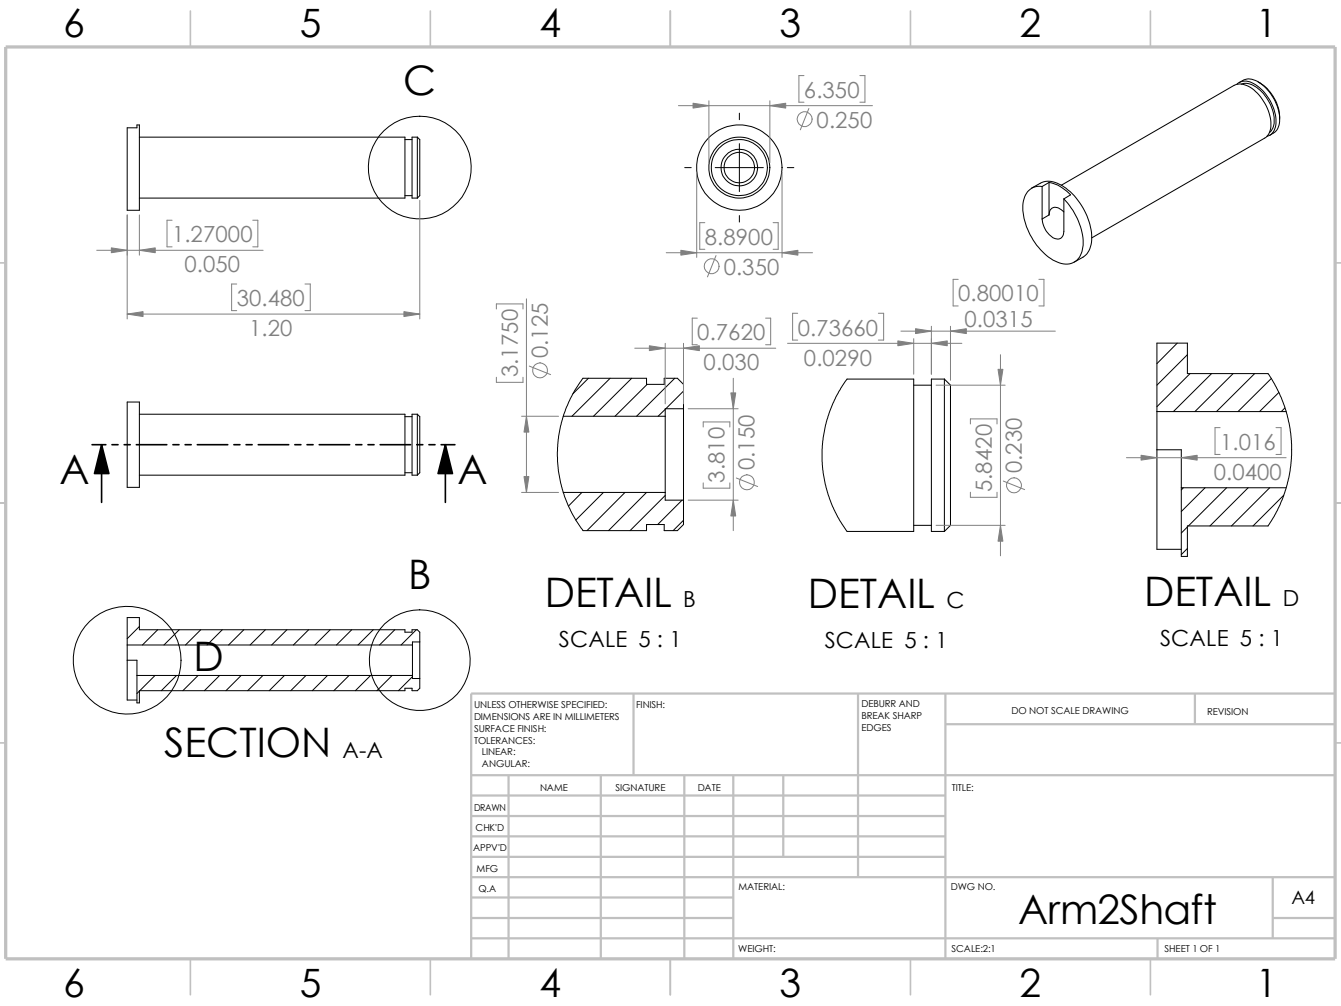
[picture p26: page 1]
SCALE:2:1; WEIGHT:; REVISION; SHEET 1 OF 1; FINISH:; EDGES; DEBURR AND BREAK SHARP; SECTION A-A; DETAIL C; SCALE 5 : 1; DETAIL B; SCALE 5 : 1 3.810 0.150; DETAIL D

UNLESS OTHERWISE SPECIFIED:
DIMENSIONS ARE IN MILLIMETERS
SURFACE FINISH:
TOLERANCES:
LINEAR:
ANGULAR:

DO NOT SCALE DRAWING

NAME | SIGNATURE | DATE | | | | TITLE:

DRAWN
CHK'D
APPV'D
Q.A | | | | MATERIAL: | DWG NO. Arm2Shaft | A4

MFG

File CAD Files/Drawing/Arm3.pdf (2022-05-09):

6

5

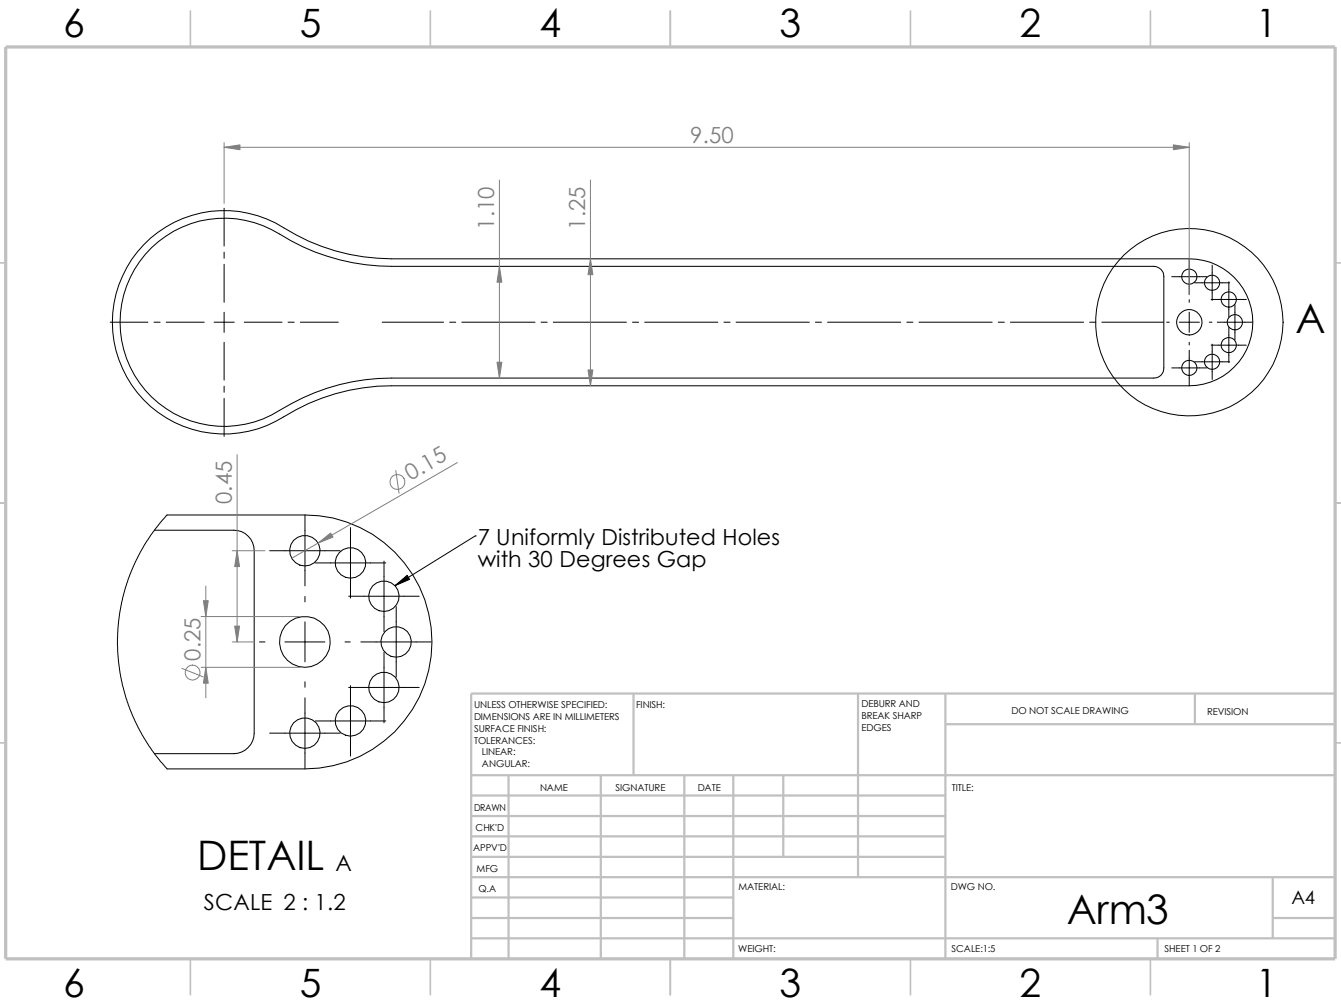
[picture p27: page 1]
SCALE; DETAIL; SCALE:1:5; WEIGHT:; REVISION; SHEET 1 OF 2; FINISH:; EDGES; DEBURR AND BREAK SHARP

with 30 Degrees Gap ⁰.45 0.25

7 Uniformly Distributed Holes

UNLESS OTHERWISE SPECIFIED:
DIMENSIONS ARE IN MILLIMETERS
SURFACE FINISH:
TOLERANCES:
LINEAR:
ANGULAR:

DO NOT SCALE DRAWING

NAME | SIGNATURE | DATE | | | | TITLE:

DRAWN
CHK'D
APPV'D
Q.A | | | | MATERIAL: | DWG NO. Arm3 | A4

MFG

0.35

B B

SECTION B-B; SCALE 1 : 1.2 ⁰.50; WEIGHT:; SCALE:1:5; SHEET 2 OF 2; REVISION; FINISH:; EDGES; DEBURR AND BREAK SHARP

DO NOT SCALE DRAWING UNLESS OTHERWISE SPECIFIED:
DIMENSIONS ARE IN MILLIMETERS
SURFACE FINISH:
TOLERANCES:
LINEAR:
ANGULAR:

NAME | SIGNATURE | DATE | | | | TITLE:

DRAWN
CHK'D
APPV'D

MFG
Q.A | | | | MATERIAL: | DWG NO. Arm3 | A4

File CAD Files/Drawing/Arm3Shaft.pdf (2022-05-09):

6

5

WEIGHT:; SCALE:2:1; SHEET 1 OF 1; REVISION; FINISH:; EDGES; DEBURR AND BREAK SHARP; DETAIL A; SCALE 7.5 : 1

DO NOT SCALE DRAWING UNLESS OTHERWISE SPECIFIED:
DIMENSIONS ARE IN MILLIMETERS
SURFACE FINISH:
TOLERANCES:
LINEAR:
ANGULAR:

NAME | SIGNATURE | DATE | | | | TITLE:

DRAWN
CHK'D
APPV'D

MFG
Q.A | | | | MATERIAL: | DWG NO. Arm3Shaft | A4

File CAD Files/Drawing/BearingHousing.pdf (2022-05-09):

30.480

0.787 0.825

4 Through Holes for M6 Bolts; SHEET 1 OF 2; WEIGHT:; SCALE:1:1; REVISION; FINISH:; EDGES; DEBURR AND BREAK SHARP

UNLESS OTHERWISE SPECIFIED:
DIMENSIONS ARE IN MILLIMETERS
SURFACE FINISH:
TOLERANCES:
LINEAR:
ANGULAR:

DO NOT SCALE DRAWING

NAME | SIGNATURE | DATE | | | | TITLE:

DRAWN
CHK'D
APPV'D

MFG
Q.A | | | | MATERIAL: | DWG NO. BearingHousing | A4

6

5

2 Threaded Holes for 2-56 Bolts; SCALE:1:1; WEIGHT:; REVISION; SHEET 2 OF 2; FINISH:; EDGES; DEBURR AND BREAK SHARP

UNLESS OTHERWISE SPECIFIED:
DIMENSIONS ARE IN MILLIMETERS
SURFACE FINISH:
TOLERANCES:
LINEAR:
ANGULAR:

DO NOT SCALE DRAWING

NAME | SIGNATURE | DATE | | | | TITLE:

DRAWN
CHK'D
APPV'D
Q.A | | | | MATERIAL: | DWG NO. BearingHousing | A4

MFG

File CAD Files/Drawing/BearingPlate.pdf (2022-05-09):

6

5

SHEET 1 OF 1; WEIGHT:; SCALE:1:1; DO NOT SCALE DRAWING; REVISION; FINISH:; EDGES; DEBURR AND BREAK SHARP

5 Through Holes for
2-56 Bolts

Radius Determined by Mill Size

UNLESS OTHERWISE SPECIFIED:
DIMENSIONS ARE IN MILLIMETERS
SURFACE FINISH:
TOLERANCES:
LINEAR:
ANGULAR:

NAME | SIGNATURE | DATE | | | | TITLE:

DRAWN
CHK'D
APPV'D
Q.A | | | | MATERIAL: | DWG NO. BearingPlate | A4

MFG

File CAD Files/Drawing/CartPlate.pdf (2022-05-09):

6

5

DO NOT SCALE DRAWING; REVISION; SHEET 1 OF 1; WEIGHT:; SCALE:1:2; EDGES; FINISH:; DEBURR AND BREAK SHARP; CartPlate ¹⁸.860 72.280; SECTION A-A ⁵.00

UNLESS OTHERWISE SPECIFIED:
DIMENSIONS ARE IN MILLIMETERS
SURFACE FINISH:
TOLERANCES:
LINEAR:
ANGULAR:

NAME | SIGNATURE | DATE | | | | TITLE:

DRAWN
CHK'D
APPV'D

MFG
Q.A | | | | MATERIAL: | DWG NO. | A4

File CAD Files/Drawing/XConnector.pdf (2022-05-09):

6

5

REVISION; TITLE:; SHEET 1 OF 1; WEIGHT:; SCALE:1:1; SIGNATURE; DATE DRAWN; FINISH:; EDGES; NAME; DEBURR AND BREAK SHARP; 8 Through Holes

UNLESS OTHERWISE SPECIFIED:
DIMENSIONS ARE IN MILLIMETERS
SURFACE FINISH:
TOLERANCES:
LINEAR:
ANGULAR:

DO NOT SCALE DRAWING

CHK'D
APPV'D

MFG
Q.A | MATERIAL: | DWG NO. XConnector | A4
